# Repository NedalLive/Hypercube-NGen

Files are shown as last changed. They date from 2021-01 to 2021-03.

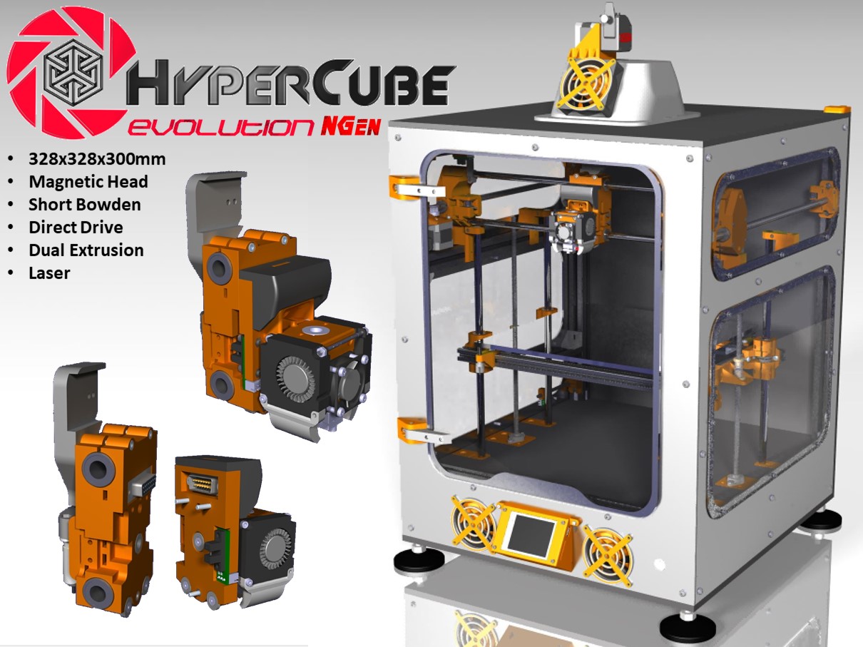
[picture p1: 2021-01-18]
Hypercube NGEN V2/images/Montage Hypercube V2.jpg

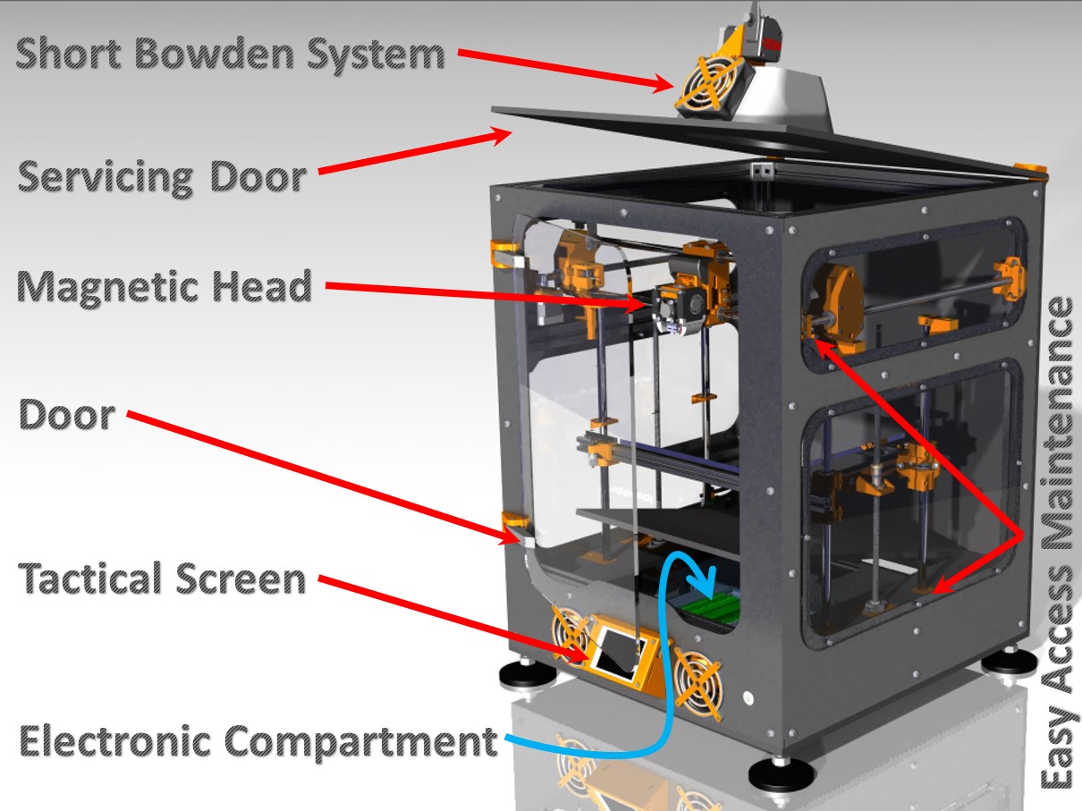
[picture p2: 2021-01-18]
Hypercube NGEN V2/images/montage Hypercube V22.jpg

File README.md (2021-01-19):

Logo Ngen

### **La Machine:**
Capture3

### Les têtes d'origine
Ngen V2 All Head Front

### Hypercube Ngen (NedalLive Genertion) 300x300x300

* Bowden Court de 400mm.
* Caisson fermé integralement.
* Tête Magnétique à remplacement rapide
* MultiTêtes develloppées par la communauté
* Bowden
* Direct Drive BMG, Titan aero et Hemera
* Hotend E3DV6
* Hotend AIO
* Hotend Dragon
* Gravage Laser
* Evolution constante

Un kit châssis disponible sur le site http://www.systeal.com/fr/kits-imprimantes-3d/1242-kit-hypercube-evo-ngen.html
Les plaques Dibond peuvent être commandées chez https://gen3d.fr/categoaquarie-produit/plge-hypercube-ngen/

Hypercube Ngen C'est vous, C'est nous! continuons à faire évoluer la machine !
Les idées les plus folles sont les bienvenues:
https://www.facebook.com/groups/hypercubeevolutionfr/
https://www.facebook.com/groups/Hypercubeevolution/

Pour conclure : je tiens à rappeler que nous sommes bénévoles et que ce n'est pas notre travail, nous sommes comme vous tous qui passez par ici, je vous remercie donc par avance pour votre bienveillance et votre participation active à l'évolution du bébé.

Pour me Soutenir:



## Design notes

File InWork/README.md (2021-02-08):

__Le contenu de ce dossier n'est pas encore Partagé, il est reservé à l'equipe de Dev. c'est à vos risques et periles !__

## Pour les Developpeurs
Creer un dossier pour chaques sujet en cour de Dev.
Y ajouter un README.md qui contien une explication succinte du projet en cours

## Explication de l'arborescence des Repères
Les N° de Repere de 0001 a 0999 sont des pièces Fabriquées
Les N° de Repere de 1000 à 9999 sont des Elements standards (acheter)

* A001 - Chassis
  * C001 Support Poulie AV V2
  * C002 Suppor Poulie AR V2

* A002 - Plateau
  * D00x - Reservé Dev Lié au plateau

* A003 - Axe Y
  * E00x - Reservé aux Dev liés à l'axe Y

* A004 - Axe X
  * B001 Chariot X
  * B002 Tête Piezo Orion E3DV6
  * B003 Tête E3DV6 standard
  * B004 Tête AIO Standard
  * B005 Tête Laser
  * B006 Tête Dragon

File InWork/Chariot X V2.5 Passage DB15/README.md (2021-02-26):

Simple modification pour pouvoir passer la prise DB15 DEJA CABLEE, au travers du chariot, en cas de changement (casse d'un élement du chariot).

Cela évite une étape "simple" mais très fastidieuse, le décablage total de la tête d'impression c.a.d. débrancher sur la carte mère, sortir les cables des passages de cables, des chaines, passer au travers du chariot, puis la même dans l'autre sens)
Quand on a un caisson, c'est un "life saver"

Il ya 2 versions : 
- V2, pour ceux qui ont des capteurs piezzo
- V1, pour ceux qui comme moi sont sur une V1 bltouch et n'ont pas l'intention de migrer vers la V2 dans l'immédiat.

La version V1 a été "améliorée" :
- relookage pour ressembler à la V2
- création de passages pour des boutons de serrage de roulement, sur la vis des aimants inférieurs  (le step des boutons est inclus)
- prévu pour les aimants supermagnete CS-S-15-04-N

NOTA : il y a une paroi fine, pour l'écrou de l'aimant central, à voir si ça peut s'imprimer correctement (pour la V1 ça passe !)

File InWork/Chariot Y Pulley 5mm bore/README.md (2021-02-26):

Modification des chariots Y :

Utilisation de poulies (de marques Mellow) 2GT alésage de 5mm pour courroie de 6mm

Alignement des poulies des chariots Y avec les nouveaux supports de poulies AV/AR

Assurez vous d'avoir une imprimante bien calibrée:

Réglage des steps de l'extrudeur

Réglage du débit de l'extrudeur

Réglage recommandé du Slicer:

Buse : 0,4mm

Hauteur de couche : 0,20mm

Nombre de périmètre : 4

Remplissage : 25%

Attention au sens d'impression des chariots, regardez la capture d'écran disponible montrant le sens d'impression

Modification of Y carriages:

Use of pulleys (Mellow brands) 2GT 5mm bore for 6mm belt

Alignment of carriage pulleys with new front / rear pulley brackets

Make sure you have a well calibrated printer:

Adjustment of extruder steps

Adjustment of extruder flow

Recommended slicer setting:

Nozzle: 0.4mm

Layer height: 0.20mm

Number of perimeter: 4

Infill: 25%

Pay attention to the printing direction of the carriages, see the screenshot available showing the printing direction

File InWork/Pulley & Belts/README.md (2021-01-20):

## Dev Poulies Courroies
* Demultiplication 20/30 dents
* Transfert des moteur à l'arriere sur SilentBlock
* ReDesign des supports poulies AR et AV
* Passage de toute les poulies sur Diametre interieur 5mm

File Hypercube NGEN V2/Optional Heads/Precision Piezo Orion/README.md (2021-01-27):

https://www.thingiverse.com/thing:4014481

compatible NGEN V2 en enlevant le endstop

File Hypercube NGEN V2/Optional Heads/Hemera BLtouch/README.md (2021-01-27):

Hemera for HEVO NGEN first generation by pipersw on Thingiverse: https://www.thingiverse.com/thing:4695196

Based on "E3d Hemera Mount for Precision Orion Piezo - Hypercube Evolution - HEVOHemera Piezo Orion for NGEN first gen"
https://www.thingiverse.com/thing:4694110
I design my own head for E3D Hemera/ Trianglelabs matrix extruder for the HEVO NGEN first generation.

The fan shroud is just take from "5015 Hemera Fan Shroud with BLTouch bracket" https://www.thingiverse.com/thing:4588159

The Offset position of the bltouch will be: X-24.50 Y-44.00 Z-0.95

The Hemera model is from "E3D Hermes / Hemera CAD (V6&Volcano)" https://www.thingiverse.com/thing:4025946

The Matrix extruder is more or less a clone of the hemera extruder. The position of the nozzle is not exactly the same.
5015 Fan Shroud for Matrix Extruder https://www.thingiverse.com/thing:4722064

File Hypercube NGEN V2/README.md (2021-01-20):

### la têtes principale V2 vue en coupe
TETE PIEZO COUPEE

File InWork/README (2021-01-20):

## Dossier de travail des developpeur##
Le contenue de ce dossier n'est pas encore Partagé c'est à vos risques et periles !

##Pour les Developpeur##
Creer un dossier pour chaques sujet en cour de Dev
Y ajouter un README qui contien une explication succinte du projet en cours

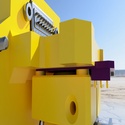
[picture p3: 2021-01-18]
Hypercube NGEN V2/Optional Heads/Precision Piezo Orion/images/large_thumb_2.jpg

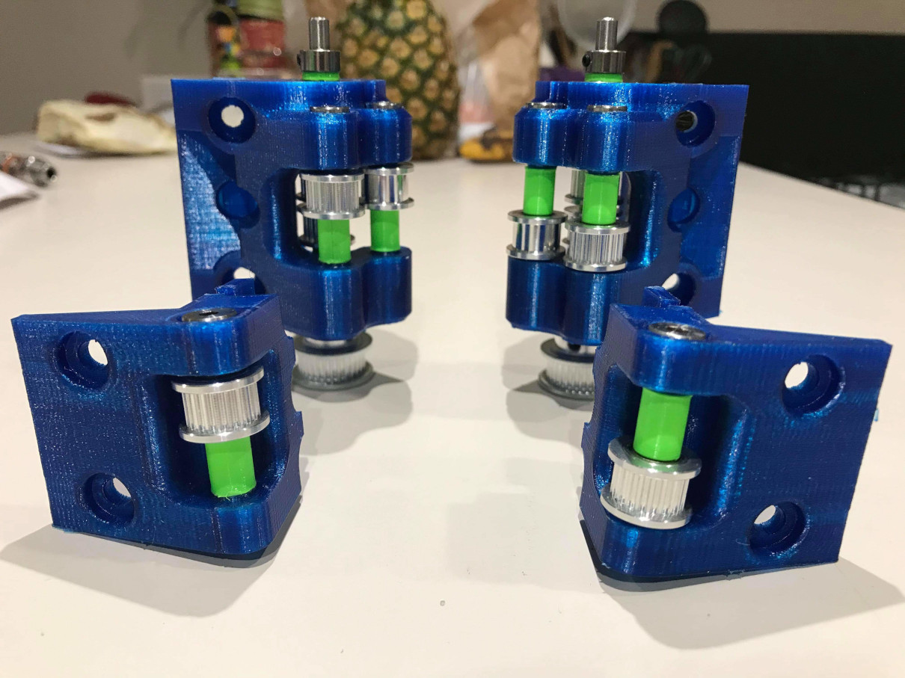
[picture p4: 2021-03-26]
InWork/Pulley & Belts/Images/vue de 4 supports.jpeg

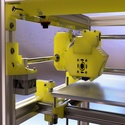
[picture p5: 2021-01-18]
Hypercube NGEN V2/Optional Heads/Precision Piezo Orion/images/large_thumb_9.jpg

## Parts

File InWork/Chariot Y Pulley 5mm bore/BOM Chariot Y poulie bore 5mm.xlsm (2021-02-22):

Désignations | Quantité | Liens d'achat
Vis epaulée Diametre 5 M4 x 25mm (25mm longeur de l'épaulement) | 4 | https://fr.aliexpress.com/item/4000704090811.html?spm=a2g0o.cart.0.0.47e73c00lnQyEg&mp=1
Ecrou M4 | 4 | https://fr.aliexpress.com/item/32977174437.html
Poulie Mellow GT2 6mm alésage 5mm 20 dents | 2 | https://fr.aliexpress.com/item/33023133633.html?spm=a2g0o.cart.0.0.1a143c00NBzYn4&mp=1
Poulie Mellow GT2 6mm alésage 5mm sans dent | 2 | https://fr.aliexpress.com/item/33023133633.html?spm=a2g0o.cart.0.0.1a143c00NBzYn4&mp=1

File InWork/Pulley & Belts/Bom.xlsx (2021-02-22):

support poulie AR LR | Qté | Lien
Bering 625zz | 4 | https://fr.aliexpress.com/item/32816424545.html
Axe Diam 5 L90mm | 2 | https://fr.aliexpress.com/item/1005001279496068.html
Vis epaulé D5x40 M4 | 4 | https://fr.aliexpress.com/item/4000704090811.html?spm=a2g0o.cart.0.0.28963c00ZiA8Oa&mp=1
Ecrou M4 | 4 | https://fr.aliexpress.com/item/32798773566.html
Poulie libre Gates 20T Bore 5 | 4 | https://fr.aliexpress.com/item/33023133633.html
Poulie libre Gates 20WT Bore 5 | 2 | https://fr.aliexpress.com/item/33023133633.html
Poulie Fixe Gates 20T Bore 5 | 2 | https://fr.aliexpress.com/item/4001045520299.html?spm=a2g0s.9042311.0.0.7a326c37pw91rd
Poulie Fixe Gates 30T Bore 5 | 2 | https://fr.aliexpress.com/item/4001308821466.html?spm=a2g0o.cart.0.0.28963c00ZiA8Oa&mp=1
Anneau de verouillage D5 x7.5mm | 2 | https://fr.aliexpress.com/item/32900283591.html?scm_id=1007.14976.205978.0&scm-url=1007.14976.205978.0&_t=gps
Vis M3x18 | 4
Ecrou M3 | 4
Courroie GT2 Close L154mm (ou entre 150 et 160) | 2 | https://fr.aliexpress.com/item/4000311901856.html
Amortisseur Nema17 | 2 | https://www.aliexpress.com/item/4000114726218.html?spm=a2g0s.9042311.0.0.2cc84c4dCTUro2
Spacer 72 | 4 | imprimé
Spacer 73 | 4 | imprimé
Spacer 74 | 2 | imprimé
Spacer 75 | 4 | imprimé
Support Poulie AV LR
Vis épaulé D5x30 M4 | 2 | https://fr.aliexpress.com/item/4000704090811.html?spm=a2g0o.cart.0.0.28963c00ZiA8Oa&mp=1
Poulie Libre 20T Bore 5 | 2 | https://fr.aliexpress.com/item/33023133633.html
Ecrou M4 | 2 | https://fr.aliexpress.com/item/32798773566.html
Vis M3x18 | 4
Ecrou M3 | 4
Spacer 73 | 2 | imprimé

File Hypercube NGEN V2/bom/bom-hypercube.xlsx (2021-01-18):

BOM BY MICHAEL HAM | will not be kept up to date / For Information
designation | for information | quantité | reference | fournisseur | lien | PRIX | remarque
ventilateur moteur | 50mm 12vdc | 2 |  |  | https://fr.aliexpress.com/item/New-Plastic-DC-12V-2-Pins-Connector-Brushless-Cooling-Fan-50mm-x-50mm-x-10mm/32747373317.html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 | 1.6
boutton on/off | m16 | 1 | 220vac |  | https://fr.aliexpress.com/item/1PCS-YT1211-Hole-Size-16-mm-Self-locking-Latching-switch-Metal-push-button-switch-With-LED/32789229044.html | 4.14
connecteur db15f |  | 1 | d-sub DB15F |  | https://fr.aliexpress.com/item/Promotion-DB15-15-Pin-Female-to-Male-Solder-Type-Adapter-Connectors-5-Pair/32623042100.html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 | 1.79
connecteur db15m |  | 1 | d-sub DB15M |  |  | 0 | en kit au dessus
bornier |  | 5x10 | UK2,5N | LEGRAND | https://fr.aliexpress.com/item/10Pcs-UK-3N-Instead-of-PHOENIX-CONTACT-Terminal-Blocks-DIN-Rail-Universal-Class-Connector-Screw-Terminal/32875022823.html | 14.32
Bltouch |  | 1 |  | antclabs | https://fr.aliexpress.com/item/3D-Touch-Auto-Leveling-Sensor-Auto-Bed-Leveling-Sensor-BLTouch-For-3D-Printers-Improve-Printing-Precision/32890485972.html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 | 10.5
extrudeur |  | 1 | BMG | Bontech | https://fr.aliexpress.com/item/Prusa-i3-mk2-mk2-5-mk3-3d-imprimante-extrudeuse-engrenages-d-entra-nement-Btech-double-engrenages/32898104617.html | 10.16 | c'est les roulements le reste est a imprimer ou http://urlz.fr/7HNY ou http://urlz.fr/7HO3
E3DV6 ou AIO |  | 1 |  | E3D ou hotend,fr | https://fr.aliexpress.com/item/E3DV6-12-v-distance-0-4-1-75-4-1-gorge-tout-droit-travers-5-gorge/32895173407.html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 | 13.57
ventilateur boitier | 80mm 12vdc | 3 |  |  | https://fr.aliexpress.com/item/80-80-25-MM-Personal-Computer-Case-Cooling-Fan-DC-12V-2200RPM-45CM-Fan-Cable-PC/32785097667.html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 | 3.18
ventilateur radial | 4010 12VDC | 2 |  |  | http://urlz.fr/7HO9 | 5.52
relais ssr |  | 1 | SSR 12DC 220AC |  | https://fr.aliexpress.com/item/1pcs-solid-state-relay-SSR-25DA-25A-3-32V-DC-TO-24-380V-AC-SSR/32663806352.html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 | 2.61
dual relais |  | 1 | 5VIN 12VDC |  | https://fr.aliexpress.com/item/3-3-v-5-v-12-v-24-v-4-Canal-Relais-Module-Haute-et-faible/32880648815.html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 | 6,22/5,96 | est ce bon ? Et surtout lequel 5v ou 12 v? | 6.22
Ressort | 7,5x5x20mm | 4 |  |  | https://fr.aliexpress.com/item/10-Pcs-Carbon-Steel-Feeder-Spring-For-Makerbot-3D-Printer-Extruder-Heated-Bed-W315/32818242357.html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 | 0.91
raspberry pi3 |  | 1 |  | RASPBERRY | https://fr.aliexpress.com/item/2016-NEW-Original-Raspberry-Pi-3-Model-B-Board-1GB-LPDDR2-BCM2837-64-bit-Quad-Core/32626862737.html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 | 37.61
allimentation |  | 1 | 220AC 12DC 500W |  | https://fr.aliexpress.com/item/Szvfun-50W-Led-Driver-100w-220v-to-12v-10A-Power-Supply-12v-5A-15A-20A-30A/32843698051.html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 | 24.73
FIN DE COURSE |  | 3 | OPTICAL SENSOR |  | https://fr.aliexpress.com/item/HAILANGNIAO-6pcs-lot-Optical-Endstop-Light-Control-Limit-Optical-Switch-for-3D-Printers-RAMPS-1-4/32870806194.html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 | 2.53
RAIL DIN | 185mm | 2 | DIN |  | https://www.amazon.fr/sourcingmap%C2%AE-coulissant-Design-montage-Coupe-circuit/dp/B0159MTN2O | 5.22
MOTEUR |  | 5 | 17HS44001 |  | https://www.amazon.fr/TopDirect-Moteur-56-2oz-2-Phase-imprimante/dp/B075JG2MVS | 42.99
POULIE AVEC DENTS |  | 6 | GT2 W6 B3 20T |  | https://fr.aliexpress.com/item/GT2-Poulie-16-20-Sans-Dents-Poulie-16-20-Dents-OU-Sans-Dents-Pignon-de-distribution/32856650625.html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 | 3.66 | 20t 3x6 with
POULIE SANS DENTS |  | 2 | GT2 W6 B3 WT |  | https://fr.aliexpress.com/item/GT2-Poulie-16-20-Sans-Dents-Poulie-16-20-Dents-OU-Sans-Dents-Pignon-de-distribution/32856650625.html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 | 1.22 | 20t 3x6 without
POULIE MOTEUR |  | 2 | GT2 20T |  | https://fr.aliexpress.com/item/Gt2-Poulie-20-dents-Al-sage-5mm-6mm-6-35mm-8mm-pour-Largeur-6mm-GT2-synchrone/32881567459.html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 | 2x 3,16 | prendre en 2 x 3 pour eviter les fdp
CARTE MERE REARM RAMP 1,6 |  | 1 | REARM + RAMP1,6 |  | https://fr.aliexpress.com/item/Rampes-1-6-carte-de-mise-niveau-base-sur-Rampes-1-4-1-5-Mega-2560/32855234226.html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 | 31.37 | a4988 ou 52,94€ pour des tmc2208
ECRAN TFT3,2 |  | 1 | TFT32 | MKS | https://fr.aliexpress.com/item/CE-RoHS-3D-Printer-splash-screen-MKS-TFT32-touch-screen-smart-controller-display-3-2inch-support/32808866999.html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 | 25.76
MOSFET HOTEND | 12VDC 12/24VDC | 1 |  | MKS MOSFET | https://fr.aliexpress.com/item/3D-printer-parts-heating-controller-MKS-MOSFET-for-heat-bed-extruder-MOS-module-exceed-30A-support/32753129988.html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 | 7.67 | ou 2,70 ici =>https://fr.aliexpress.com/item/New-Hot-3D-Printer-Accessories-Mosfet-Heated-Bed-Power-Module-MKS-for-Anet-A8-A6-A2/32890179872.html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
AIMANT PLAT FRAISE | ⌀12x3 | 3 | 41-243-12 | EMILE MAURIN | https://fr.aliexpress.com/item/10-Pieces-pack-12-x-3-mm-Magnet-Strong-Neodymium-Magnets-Permanent-N50-Magnetic-Materials/32811494867.html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 | 18,4/3,13 | (version EMILE MAURIN) / (version aliexpress)
SUPPORT POUR AIMANT | ⌀12x2 | 3 | 41-600-12 | EMILE MAURIN | https://fr.aliexpress.com/item/50pcs-12mmx2mm-12X2mm-Super-Strong-Round-Disc-Rare-Earth-Neodymium-magnet-12-2-NEW-Art-Craft/32807408402.html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 | 5,55/1,66 | (version EMILE MAURIN) / a percer(version aliexpress)ou des rondelles fraisé
CANON DE GUIDAGE | ⌀2,9x8 | 1 | 33-041-6 2,9 8 | EMILE MAURIN | fdp 20,1 | 7,95/? | (version EMILE MAURIN) soit total 52€ / pas trouvé sur ali
VIS BHC | M5x10 | 41 | ISO7380 |  | https://fr.aliexpress.com/item/50-PCS-ISO7380-En-Acier-Inoxydable-a2-70-M5-10-m5-x-10-Six-Pans-Creux/32841075185.html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 | 3.64
VIS BHC | M5x16 | 25 | ISO7380 |  | https://fr.aliexpress.com/item/AXK-50pcs-M5-Alloy-Steel-ISO7380-Metric-Thread-Button-Head-Hex-Socket-Cap-Screws-Round-Bolts/32869792263.html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 | 5.53
VIS BHC | M5x12 | 74 | ISO7380 |  | https://fr.aliexpress.com/item/AXK-50pcs-M5-Alloy-Steel-ISO7380-Metric-Thread-Button-Head-Hex-Socket-Cap-Screws-Round-Bolts/32869792263.html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 | 9.94 | en prendre 2
VIS BHC | M3x8 | 16 | ISO7380 |  | https://fr.aliexpress.com/item/AXK-100pcs-Grade10-9-iso7380-M3-3-4-5-6-8-10-12-14-16-18/32870504082.html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 | 1.21
VIS BHC | M3x30 | 8 | ISO7380 |  | https://fr.aliexpress.com/item/100pcs-Grade10-9-iso7380-M3-3-4-5-6-8-10-12-14-16-18-20/32781852232.html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 | 3.34
VIS BHC | M3x25 | 2 | ISO7380 |  | https://fr.aliexpress.com/item/100pcs-Grade10-9-iso7380-M3-3-4-5-6-8-10-12-14-16-18-20/32781852232.html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 | 3.34
VIS BHC | M3x20 | 37 | ISO7380 |  | https://fr.aliexpress.com/item/100pcs-Grade10-9-iso7380-M3-3-4-5-6-8-10-12-14-16-18-20/32781852232.html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 | 3.15
VIS BHC | M3x16 | 36 | ISO7380 |  | https://fr.aliexpress.com/item/100pcs-Grade10-9-iso7380-M3-3-4-5-6-8-10-12-14-16-18-20/32781852232.html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 | 1.9
VIS BHC | M3x12 | 56 | ISO7380 |  | https://fr.aliexpress.com/item/100pcs-Grade10-9-iso7380-M3-3-4-5-6-8-10-12-14-16-18-20/32781852232.html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 | 2.52
VIS BHC | M2,5x16 | 2 | ISO7380 |  | https://fr.aliexpress.com/item/100PCS-ISO7380-M2-5-3-4-5-6-8-10-12-14-16-18-20-22/32803284037.html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 | 2.23
VIS BHC | M2,5x8 | 2 | ISO7380 |  | https://fr.aliexpress.com/item/100PCS-ISO7380-M2-5-3-4-5-6-8-10-12-14-16-18-20-22/32803284037.html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 | 1.48
ECROU | M3 | 105 |  |  | https://fr.aliexpress.com/item/M3-nut-M3-copper-column-matching-hex-nut-nut/32756822044.html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 | 1.74 | en prendre 2
GOUJON | M2,5x50 | 1 |  |  | https://fr.aliexpress.com/item/12-9-Level-Cylindrical-Head-Six-Angle-Bolt-M2-5-50/32721234193.html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 | 1.75 | pas obligatoire
VIS TRAPEZOIDALE Z | M8x2x395 | 2 |  |  | https://fr.aliexpress.com/item/3D-Printer-THSL-300-8D-Lead-Screw-Dia-8MM-Pitch-1mm-Lead-1mm-Length-300mm-with/32722807591.html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 | 13.7
ECROU | M2,5 | 6 |  |  | https://fr.aliexpress.com/item/50-Pcs-DIN934-M2-M2-5-M3-M4-M5-M6-M8-Noir-Nylon-crou-Hexagonal-Hexagone/32874859068.html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 | 0.75
RONDELLE 5mm | ⌀5x2,8 | 35 | ISO7089 |  | https://fr.aliexpress.com/item/100Pcs-DIN125-ISO7089-M1-6-M2-M2-5-M3-M3-5-M4-M5-M6-M8-M10/32795320300.html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 | 1.92
RONDELLE 3mm | ⌀3x0,6 | 32 | ISO7089 |  | https://fr.aliexpress.com/item/100Pcs-DIN125-ISO7089-M1-6-M2-M2-5-M3-M3-5-M4-M5-M6-M8-M10/32795320300.html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 | 1.31
VIS FHC | M3x10 | 4 | DIN7991 |  | https://fr.aliexpress.com/item/100pcs-lot-DIN7991-M3-4-5-6-8-10-12-14-16-20-Stainless-Steel-304/32785914892.html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 | 2.09
VIS FHC | M3x50 | 4 |  |  | https://fr.aliexpress.com/item/M3-DIN7991-10-9-Flat-Head-Cap-Screws-Countersunk-Head-Cap-Screws-Flat-Cup-Screws-M3/32841370184.html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 | 1.67
VIS FHC | M3x30 | 2 | DIN7991 |  | https://fr.aliexpress.com/item/50pcs-lot-DIN7991-M3-4-5-6-8-10-14-12-16-20-25-30-m3/32852869121.html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 | 2.94
T8 ECROU ANTIBACKLASH | 8x2mm | 2 |  |  |  | 0 | compris avec les vis trapezoidale
PLATEAU | 328x328x EP3 | 1 | MK2A |  | https://fr.aliexpress.com/item/2017-MK2A-300-300-3-0mm-RepRap-RAMPS-1-4-PCB-Aluminum-Heatbed-Hot-Plate-For/32811352753.html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 | 26.31
LIT CHAUFFANT SILICON | 300x300 | 1 | 220V AC |  | https://fr.aliexpress.com/item/Silicone-coussin-chauffant-chauffe-200x200-220-220-300x300mm-Puissance-160-w-280-w-360-w-500/32882403658.html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 | 20.02
PALLIER Z | ⌀8 | 2 | KFL08 |  | https://fr.aliexpress.com/item/2Pcs-KFL08-Pillow-Block-Bearing-8mm-Bore-Diameter-Zinc-Alloy-Rhombic-Flange-Bearing-For-CNC/32793159224.html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 | 2.05
ACCOUPLEMENT FLEXIBLE Z | D20L25 5x8 | 2 | RB | MISUMI | https://fr.aliexpress.com/item/1-pcs-D20L25-5X8mm-En-Alliage-D-aluminium-Z-Axe-Flexible-Accouplement-Pour-Moteur-pas-pas/32876571198.html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 | 5.38 | prendre en 2 commandes pour eviter les fdp
DOUILLE A BILLE Z |  | 8 | LM12UU | MISUMI | voir avec https://www.facebook.com/henri.rodat?sk=wall&fref=gs&dti=245503589286876&hc_location=group_dialog | 36 | 4,5*8
DOUILLE A BILLE Y |  | 2 | LM10LUU | MISUMI | fdp 3,7 | 15 | 7,5*2
DOUILLE A BILLE X |  | 4 | LM10UU | MISUMI | total 72,7 | 18 | 4,5*4
AXE DE GUIDAGE Z | ⌀12x400 | 4 | ACIER CALIBRE | MISUMI | https://fr.aliexpress.com/item/12mm-linear-shaft-200-300-350-400-440-500-560-600-650-800-mm-Chromed-Hardened/32858883464.html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 | 27.6 | ou a voir sur dold mechatronik,de https://www.dold-mechatronik.de/navi.php?a=1457&lang=eng
AXE DE GUIDAGE Y | ⌀10x450 | 2 | ACIER CALIBRE | MISUMI | https://fr.aliexpress.com/item/Optical-Axis-300-320-350-380-400-450-500-mm-Smooth-Rods-8mm-Linear-Shaft-Rail/32882612771.html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 | 12.3 | en tout 64,9 sur dold
AXE DE GUIDAGE X | ⌀10x480 | 2 | ACIER CALIBRE | MISUMI | https://fr.aliexpress.com/item/Optical-Axis-300-320-350-380-400-450-500-mm-Smooth-Rods-8mm-Linear-Shaft-Rail/32882612771.html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 | 12.6 | a recouper ou sinon au pire il peuve depasser dans le compartiment electronique
GOULOTTE ELEC | 25x25x200 | 5 |  |  | ? | ? | a prendre dans un leroymerlin
PIED | M8x50x⌀29 | 4 | PIED-D29-M8-50 | SYSTEAL |  | 0 | avec le kit
L-JOINT 3030 |  | 22 | EQ-P8-3030-INT-TPM | SYSTEAL | https://fr.aliexpress.com/item/10pcs-30-series-L-Shape-Type-Interior-Inner-Corner-Connector-Joint-Bracket-for-3030-Aluminum-Profile/32869698160.html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 | 19.86 | en prendre 3 ou alors prendre ici=> https://fr.aliexpress.com/item/20-pcs-L-Forme-Noir-Int-rieure-Coin-Connecteur-Conjointe-Support-pour-2020-3030-S-rie/32888059127.html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
EQUERRE 3030 |  | 10 | AKOYPKY6-TPM | SYSTEAL |  | 0 | avec le kit
EQUERRE2020 |  | 4 | AKOYPKY5 | SYSTEAL |  | 0 | avec le kit
T-NUT 3030 M5 |  | 100 | ECR-MA-P8-5 | SYSTEAL | https://fr.aliexpress.com/item/Free-shipping-100pcs-30-M5-hammer-nut-M5-block-t-slot-nuts-for-3030-aluminum-profile/32831895270.html | 8.66
T-NUT 2020 M5 |  | 50 | ECR-MA-P6-5 | SYSTEAL | https://fr.aliexpress.com/item/50PCS-20-m3-M4-M5-T-nut-Hammer-Head-Fasten-Nut-3D-Printer-Parts-Nickel-Plated/32909750370.html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 | 2.16
PROFILE 3030 Z | 30x30x640 | 4 | B-TYPE SLOT 8 | SYSTEAL | http://www.systeal.com/fr/kits-imprimantes-3d/1242-kit-hypercube-evo-ngen.html | 96.15
PROFILE 3030 Y | 30x30x460 | 8 | B-TYPE SLOT 8 | SYSTEAL |  | 0 | avec le kit
PROFILE 3030 X | 30x30x450 | 5 | B-TYPE SLOT 8 | SYSTEAL |  | 0 | avec le kit
PROFILE 2020 X | 20x20x446 | 2 | B-TYPE SLOT 6 | SYSTEAL |  | 0 | avec le kit
PROFILE 2020Y | 20x20x225 | 2 | B-TYPE SLOT 6 | SYSTEAL |  | 0 | avec le kit
courrroie gt2 6mm | 6mm*5m |  |  |  | https://fr.aliexpress.com/item/5m-lot-GT2-6mm-open-timing-belt-width-6mm-GT2-belt-Rubbr-Fiberglass-cut-to-length/32811832945.html | 2.8
total |  |  |  |  |  | 690.34 | il manque la goulotte

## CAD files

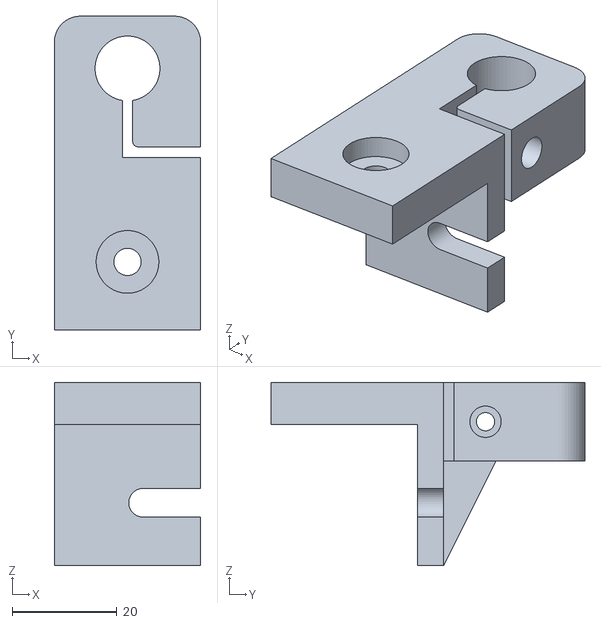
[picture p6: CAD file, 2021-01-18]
Hypercube NGEN V2/CAD/STL/A001 - ENSEMBLE CHASSIS/0020 - Z SUPPORT INF R.stl
28.0 x 60.0 x 35.0

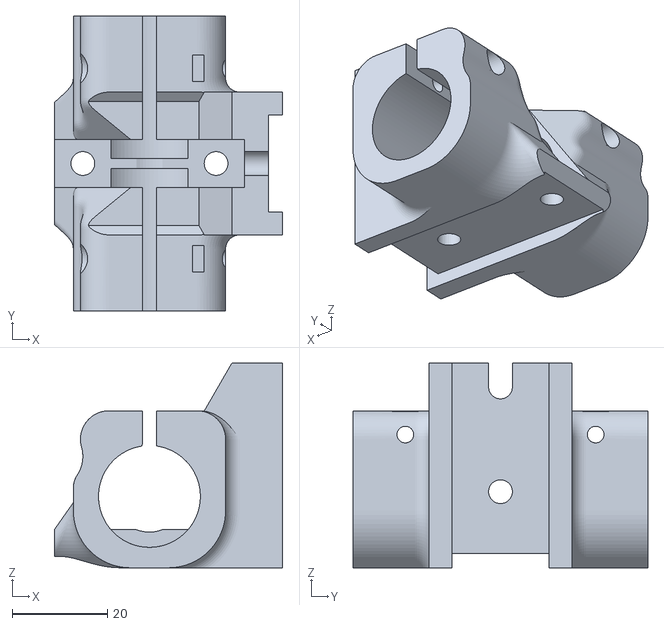
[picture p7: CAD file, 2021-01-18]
Hypercube NGEN V2/CAD/STL/A002 - ENSEMBLE PLATEAU/0023 - CHARIOT Z - LM12UU.stl
48.0 x 62.0 x 43.0

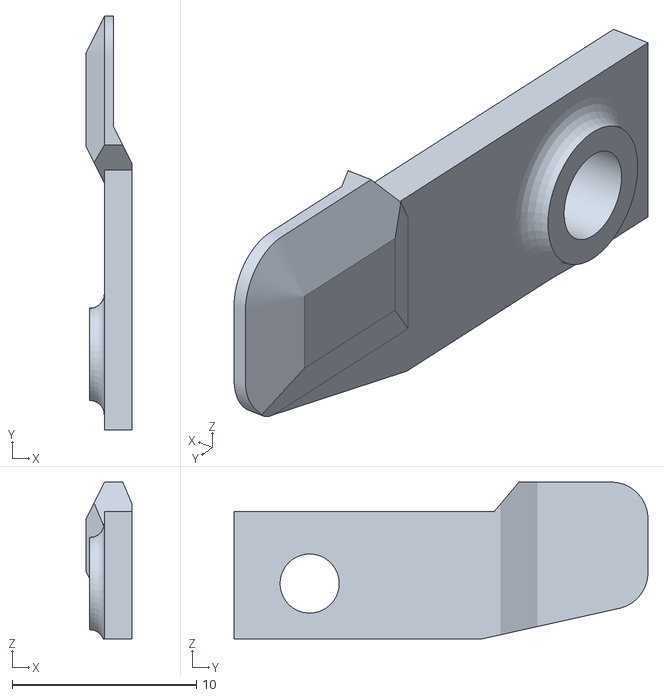
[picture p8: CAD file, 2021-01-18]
Hypercube NGEN V2/CAD/STL/A003 - ENSEMBLE AXE Y/0013 - DRAPEAU X.stl
2.50 x 22.4 x 8.50

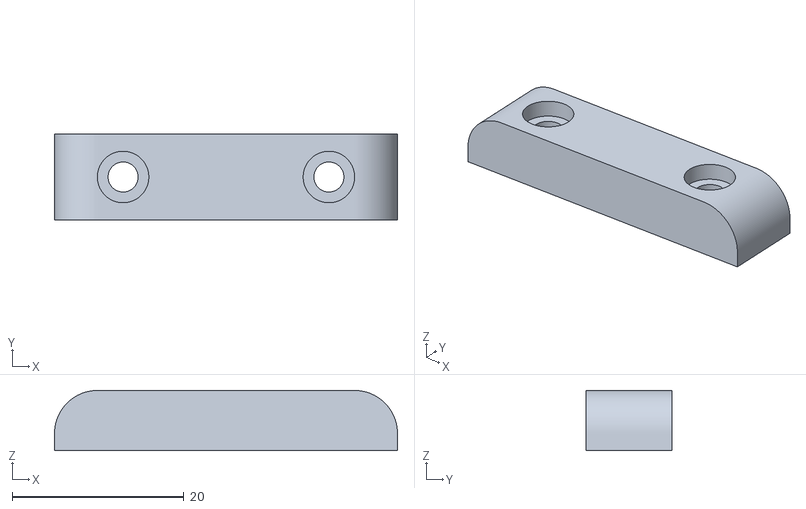
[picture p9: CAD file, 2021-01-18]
Hypercube NGEN V2/CAD/STL/A004 - ENSEMBLE AXE X/B001 - CHARIOT X V2/0002 - CLAMP.stl
40.0 x 10.0 x 7.00

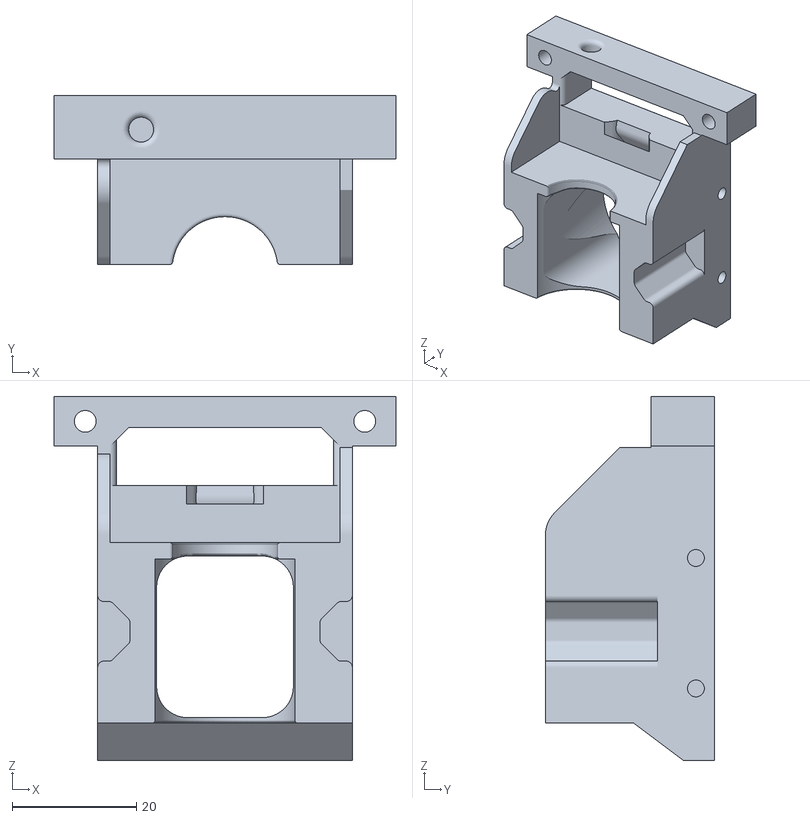
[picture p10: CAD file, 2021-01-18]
Hypercube NGEN V2/CAD/STL/A004 - ENSEMBLE AXE X/B002 - TETE PIEZO ORION/0007 - CLAMP 30mm TETE PIEZO E3DV6.stl
55.0 x 27.2 x 58.6

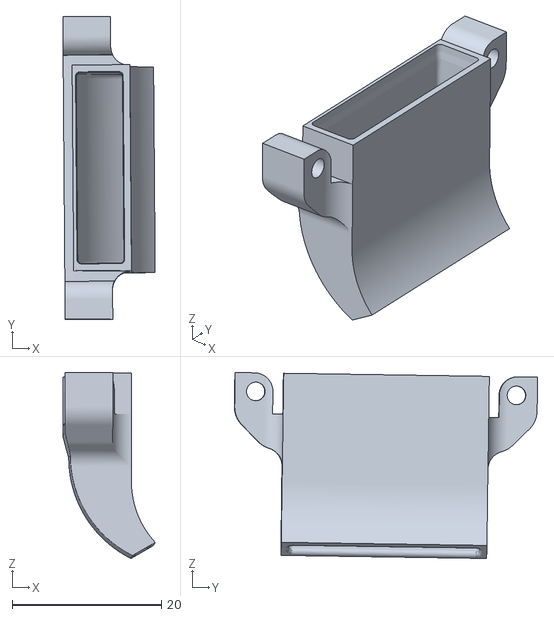
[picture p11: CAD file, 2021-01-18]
Hypercube NGEN V2/CAD/STL/A004 - ENSEMBLE AXE X/B003 - TETE E3DV6 STD V2/0009 - FAN DUCT STD.stl
12.4 x 40.7 x 25.0

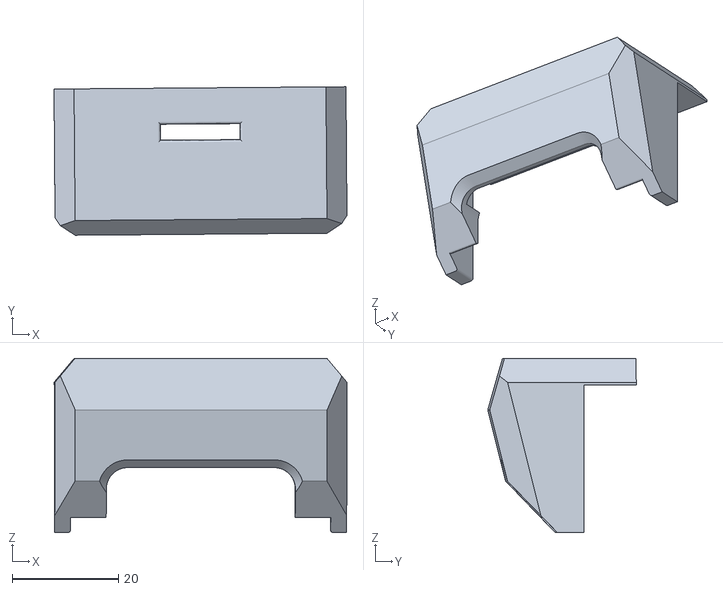
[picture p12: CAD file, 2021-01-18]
Hypercube NGEN V2/CAD/STL/A004 - ENSEMBLE AXE X/B004 - TETE AIO STD V2/0008 - CACHE STD.stl
55.2 x 28.0 x 32.8

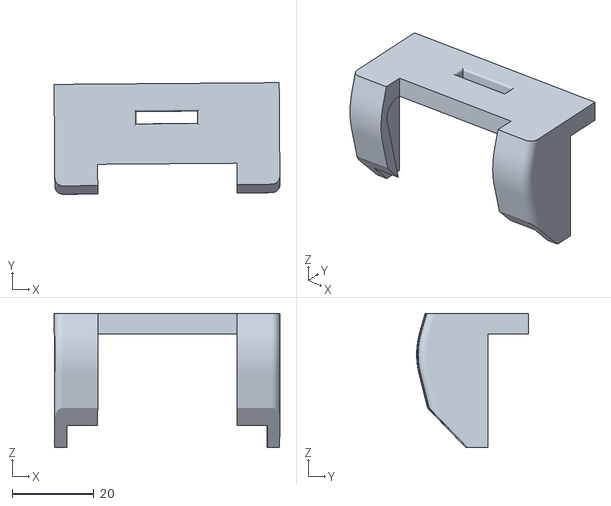
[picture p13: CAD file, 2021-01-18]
Hypercube NGEN V2/CAD/STL/A004 - ENSEMBLE AXE X/B005 - TETE LASER V2/0008 - CACHE LASER.stl
55.2 x 27.3 x 32.8

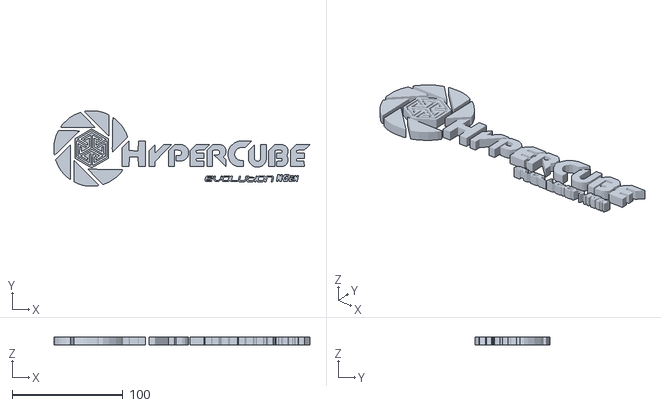
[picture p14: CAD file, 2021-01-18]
Hypercube NGEN V2/CAD/STL/HCEVO_NGEN.stl
231.1 x 67.8 x 6.98

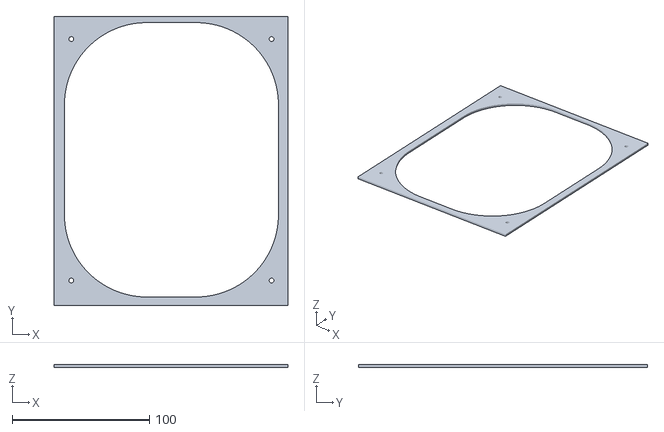
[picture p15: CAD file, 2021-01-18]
Hypercube NGEN V2/CAD/STL/Tips/PATRON DE DECOUPE PLANCHE SUP.stl
170.6 x 211.0 x 2.00

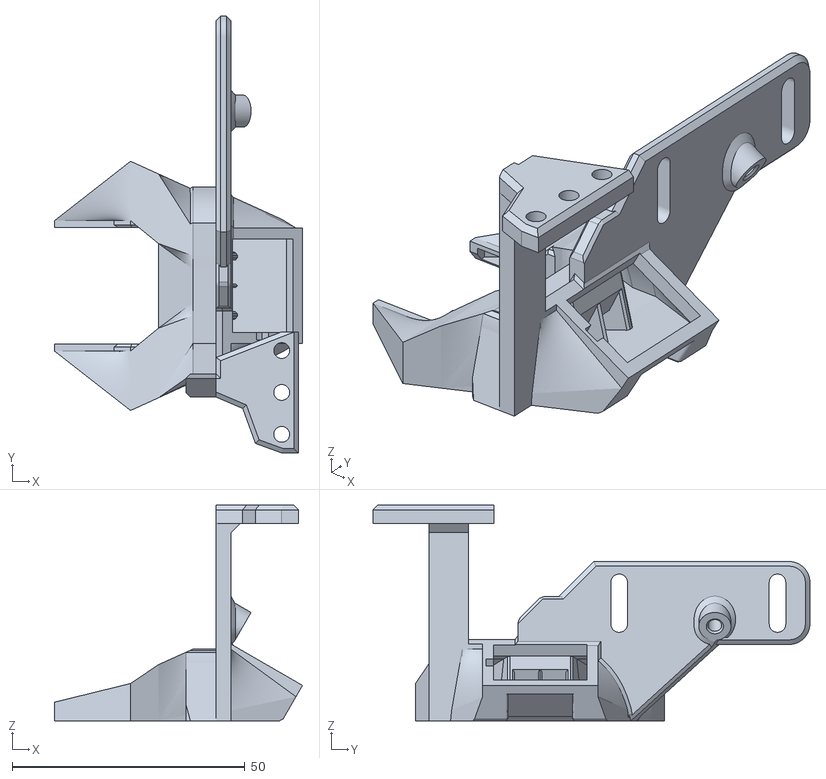
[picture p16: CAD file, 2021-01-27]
Hypercube NGEN V2/Optional Heads/Hemera BLtouch/STL/5015_Matrix_Shroud.stl
53.3 x 93.8 x 46.3

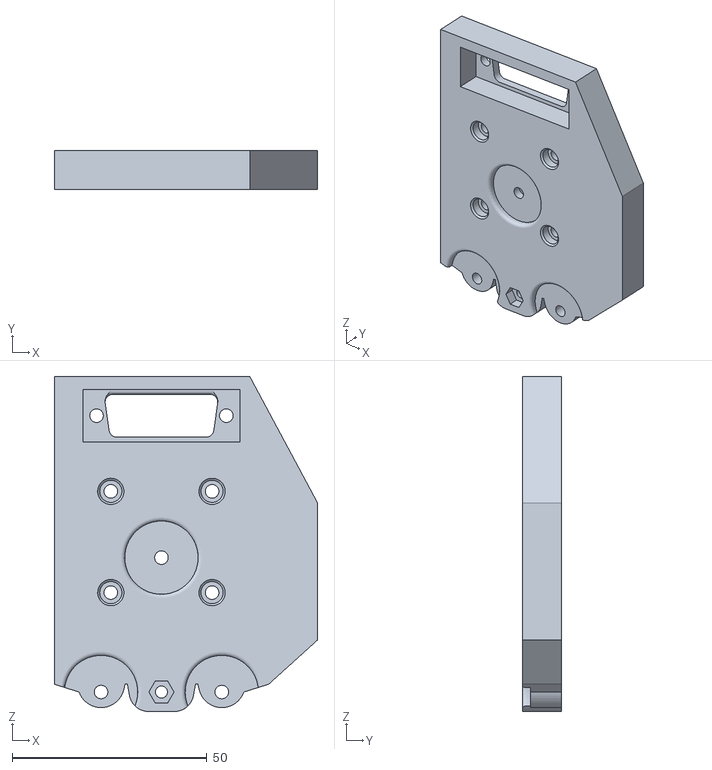
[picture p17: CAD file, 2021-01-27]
Hypercube NGEN V2/Optional Heads/Hemera Piezo Orion/STL/base Hemera piezo orion HEVO for NGEN V2.stl
67.6 x 10.0 x 86.0

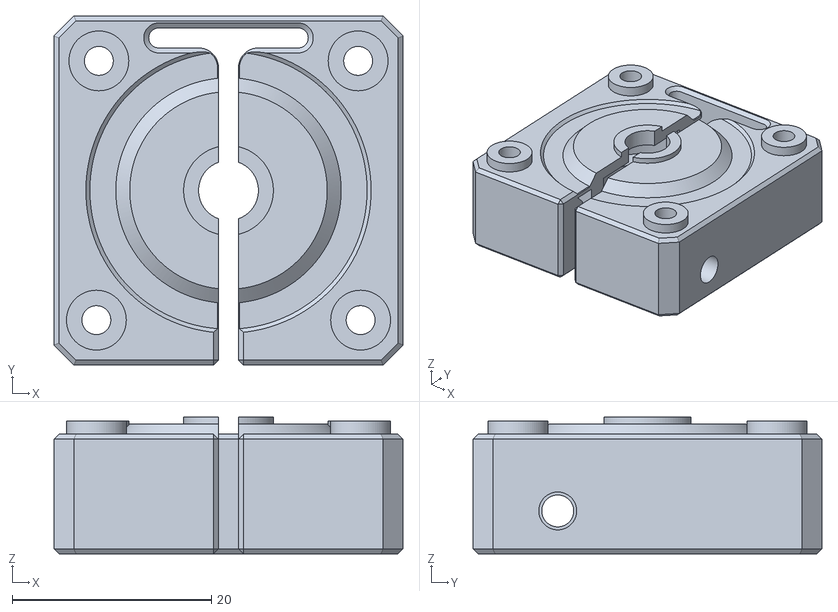
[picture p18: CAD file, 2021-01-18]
Hypercube NGEN V2/Optional Heads/Precision Piezo Orion/STL/Clamp_Precision_Orion_repaired.stl
35.0 x 35.0 x 13.7

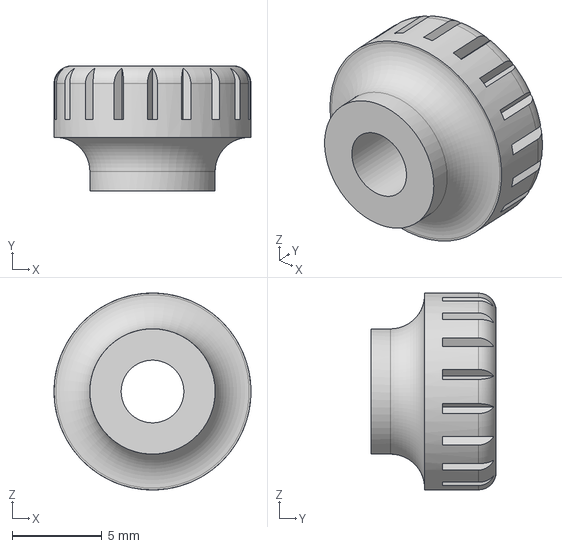
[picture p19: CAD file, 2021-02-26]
InWork/Chariot X V2.5 Passage DB15/STEP_HYPERCUBE-EVO-0001_NGENv1.5_bouton_serrage_roulement.step
11.0 x 7.00 x 11.0 mm

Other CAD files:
Hypercube NGEN V2/CAD/STL/A004 - ENSEMBLE AXE X/B006 - TETE PIEZO DRAGON V2/0007 - CLAMP 30mm TETE DRAGON V2.stl
InWork/Chariot Y Pulley 5mm bore/Chariot Y Right poulie bore 5mm.stl
InWork/Chariot Y Pulley 5mm bore/Version Step/Flag endstop X.step
InWork/Nova Hotend V1.1/STEP/HYPERCUBE-EVO-0006_NGEN_NOVA.stp
Hypercube NGEN V1/CAD/STEP/0006 - FOR DEVELLOPER.stp
Hypercube NGEN V1/CAD/STL/A001 - ENSEMBLE CHASSIS/0015 - SUPPORT MOTEUR XY L.stl
Hypercube NGEN V1/CAD/STL/A001 - ENSEMBLE CHASSIS/0016 - SUPPORT MOTEUR XY R.stl
Hypercube NGEN V1/CAD/STL/A001 - ENSEMBLE CHASSIS/0017 - SUPPORT POULIE AR L.stl
Hypercube NGEN V1/CAD/STL/A001 - ENSEMBLE CHASSIS/0018 - SUPPORT POULIE AR L.stl
Hypercube NGEN V1/CAD/STL/A001 - ENSEMBLE CHASSIS/0019 - Z SUPPORT INF L.stl
Hypercube NGEN V1/CAD/STL/A001 - ENSEMBLE CHASSIS/0021 - Z SUPPORT SUPP L.stl
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

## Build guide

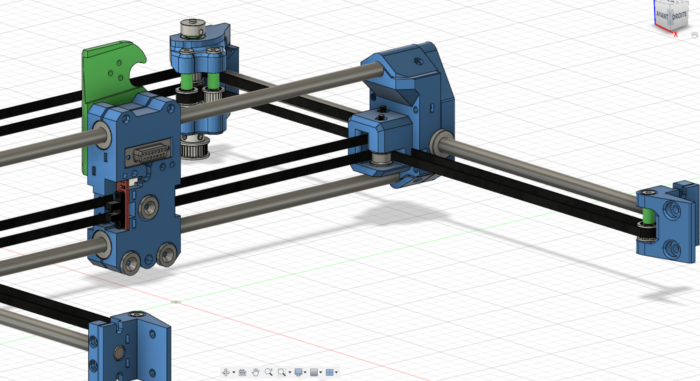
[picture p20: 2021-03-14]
InWork/Chariot Y Pulley 5mm bore/Image chariot Y/Chariot Y Right bore 5mm Assembly .png

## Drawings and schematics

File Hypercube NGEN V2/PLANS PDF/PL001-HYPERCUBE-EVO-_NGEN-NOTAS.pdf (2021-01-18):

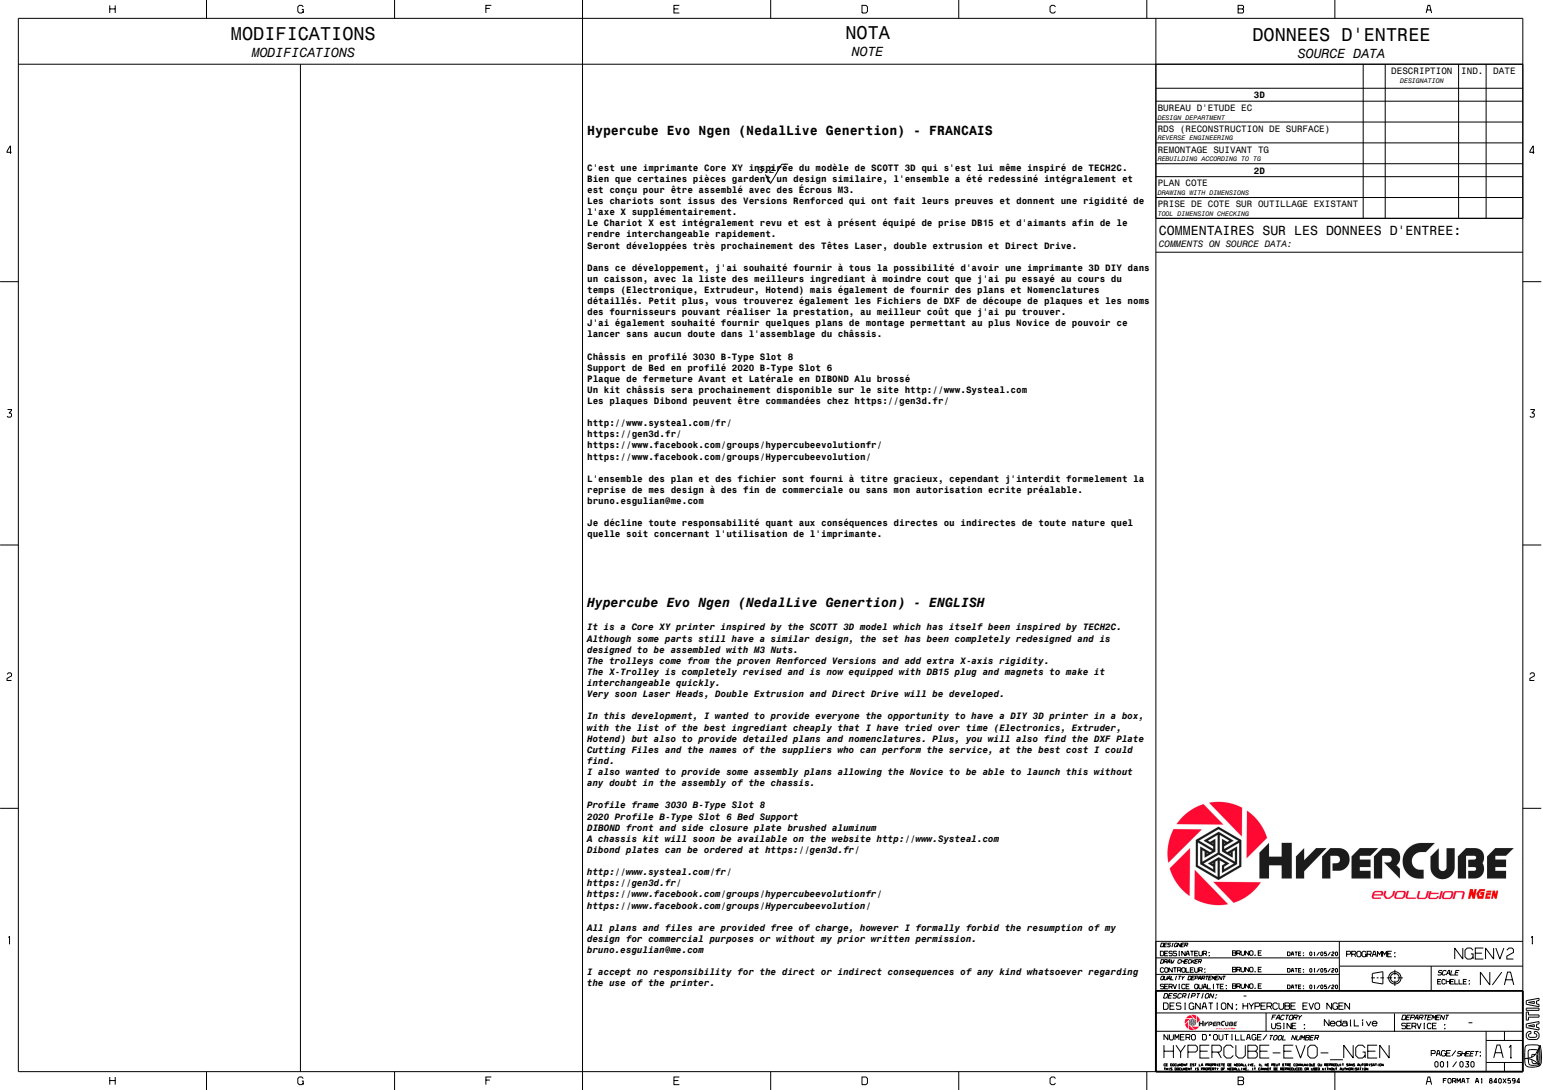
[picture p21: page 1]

MODIFICATIONS | NOTA NOTE | DONNEES D'ENTREE SOURCE DATA

DESCRIPTION DESIGNATION | IND. | DATE

BUREAU D'ETUDE EC DESIGN DEPARTMENT
RDS (RECONSTRUCTION DE SURFACE) REVERSE ENGINEERING
REMONTAGE SUIVANT TG REBUILDING ACCORDING TO TG

Hypercube Evo Ngen (NedalLive Genertion) - FRANCAIS

C'est une imprimante Core XY inspirée du modèle de SCOTT 3D qui s'est lui même inspiré de TECH2C.
Bien que certaines pièces gardent un design similaire, l'ensemble a été redessiné intégralement et
est conçu pour être assemblé avec des Écrous M3.
Les chariots sont issus des Versions Renforced qui ont fait leurs preuves et donnent une rigidité de
l'axe X supplémentairement.
Le Chariot X est intégralement revu et est à présent équipé de prise DB15 et d'aimants afin de le
rendre interchangeable rapidement.
Seront développées très prochainement des Têtes Laser, double extrusion et Direct Drive.

PLAN COTE DRAWING WITH DIMENSIONS
PRISE DE COTE SUR OUTILLAGE EXISTANT TOOL DIMENSION CHECKING

COMMENTAIRES SUR LES DONNEES D'ENTREE:
COMMENTS ON SOURCE DATA:

Dans ce développement, j'ai souhaité fournir à tous la possibilité d'avoir une imprimante 3D DIY dans
un caisson, avec la liste des meilleurs ingrediant à moindre cout que j'ai pu essayé au cours du
temps (Electronique, Extrudeur, Hotend) mais également de fournir des plans et Nomenclatures
détaillés. Petit plus, vous trouverez également les Fichiers de DXF de découpe de plaques et les noms
des fournisseurs pouvant réaliser la prestation, au meilleur coût que j'ai pu trouver.
J'ai également souhaité fournir quelques plans de montage permettant au plus Novice de pouvoir ce
lancer sans aucun doute dans l'assemblage du châssis.

Châssis en profilé 3030 B-Type Slot 8
Support de Bed en profilé 2020 B-Type Slot 6
Plaque de fermeture Avant et Latérale en DIBOND Alu brossé
Un kit châssis sera prochainement disponible sur le site http://www.Systeal.com
Les plaques Dibond peuvent être commandées chez https://gen3d.fr/

http://www.systeal.com/fr/
https://gen3d.fr/
https://www.facebook.com/groups/hypercubeevolutionfr/
https://www.facebook.com/groups/Hypercubeevolution/

L'ensemble des plan et des fichier sont fourni à titre gracieux, cependant j'interdit formelement la
reprise de mes design à des fin de commerciale ou sans mon autorisation ecrite préalable.
bruno.esgulian@me.com

Je décline toute responsabilité quant aux conséquences directes ou indirectes de toute nature quel
quelle soit concernant l'utilisation de l'imprimante.

Hypercube Evo Ngen (NedalLive Genertion) - ENGLISH

It is a Core XY printer inspired by the SCOTT 3D model which has itself been inspired by TECH2C.
Although some parts still have a similar design, the set has been completely redesigned and is
designed to be assembled with M3 Nuts.
The trolleys come from the proven Renforced Versions and add extra X-axis rigidity.
The X-Trolley is completely revised and is now equipped with DB15 plug and magnets to make it
interchangeable quickly.
Very soon Laser Heads, Double Extrusion and Direct Drive will be developed.

In this development, I wanted to provide everyone the opportunity to have a DIY 3D printer in a box,
with the list of the best ingrediant cheaply that I have tried over time (Electronics, Extruder,
Hotend) but also to provide detailed plans and nomenclatures. Plus, you will also find the DXF Plate
Cutting Files and the names of the suppliers who can perform the service, at the best cost I could
find.
I also wanted to provide some assembly plans allowing the Novice to be able to launch this without
any doubt in the assembly of the chassis.

Profile frame 3030 B-Type Slot 8
2020 Profile B-Type Slot 6 Bed Support
DIBOND front and side closure plate brushed aluminum
A chassis kit will soon be available on the website http://www.Systeal.com
Dibond plates can be ordered at https://gen3d.fr/

All plans and files are provided free of charge, however I formally forbid the resumption of my
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

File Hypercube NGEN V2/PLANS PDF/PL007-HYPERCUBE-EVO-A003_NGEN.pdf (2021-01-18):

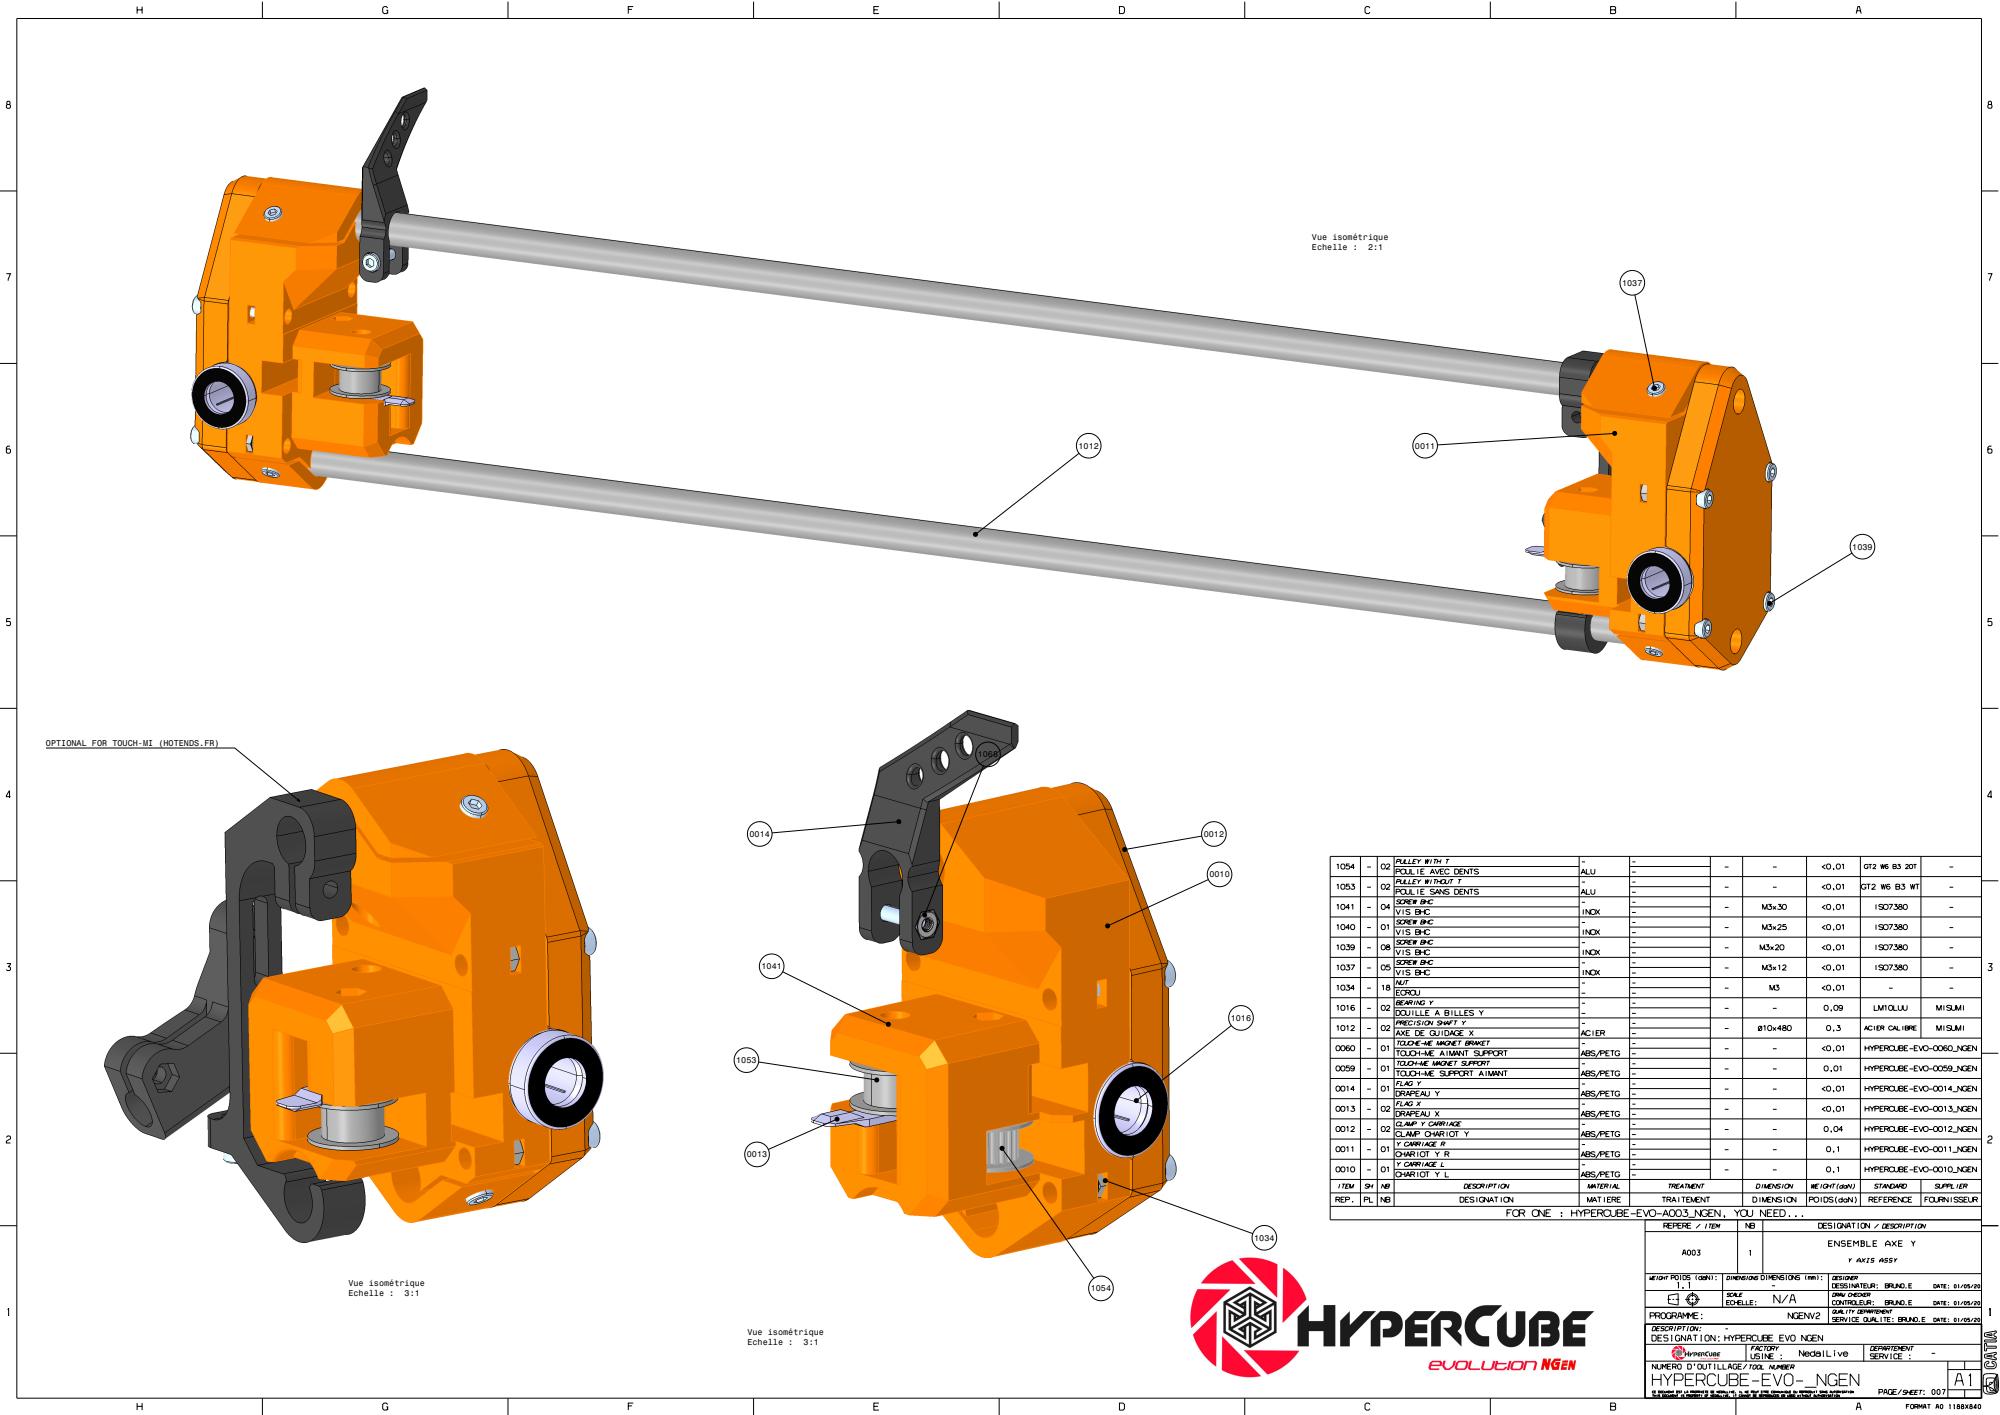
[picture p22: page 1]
Vue isométrique Echelle : 2:1; Vue isométrique Echelle : 3:1

OPTIONAL FOR TOUCH-MI (HOTENDS.FR)

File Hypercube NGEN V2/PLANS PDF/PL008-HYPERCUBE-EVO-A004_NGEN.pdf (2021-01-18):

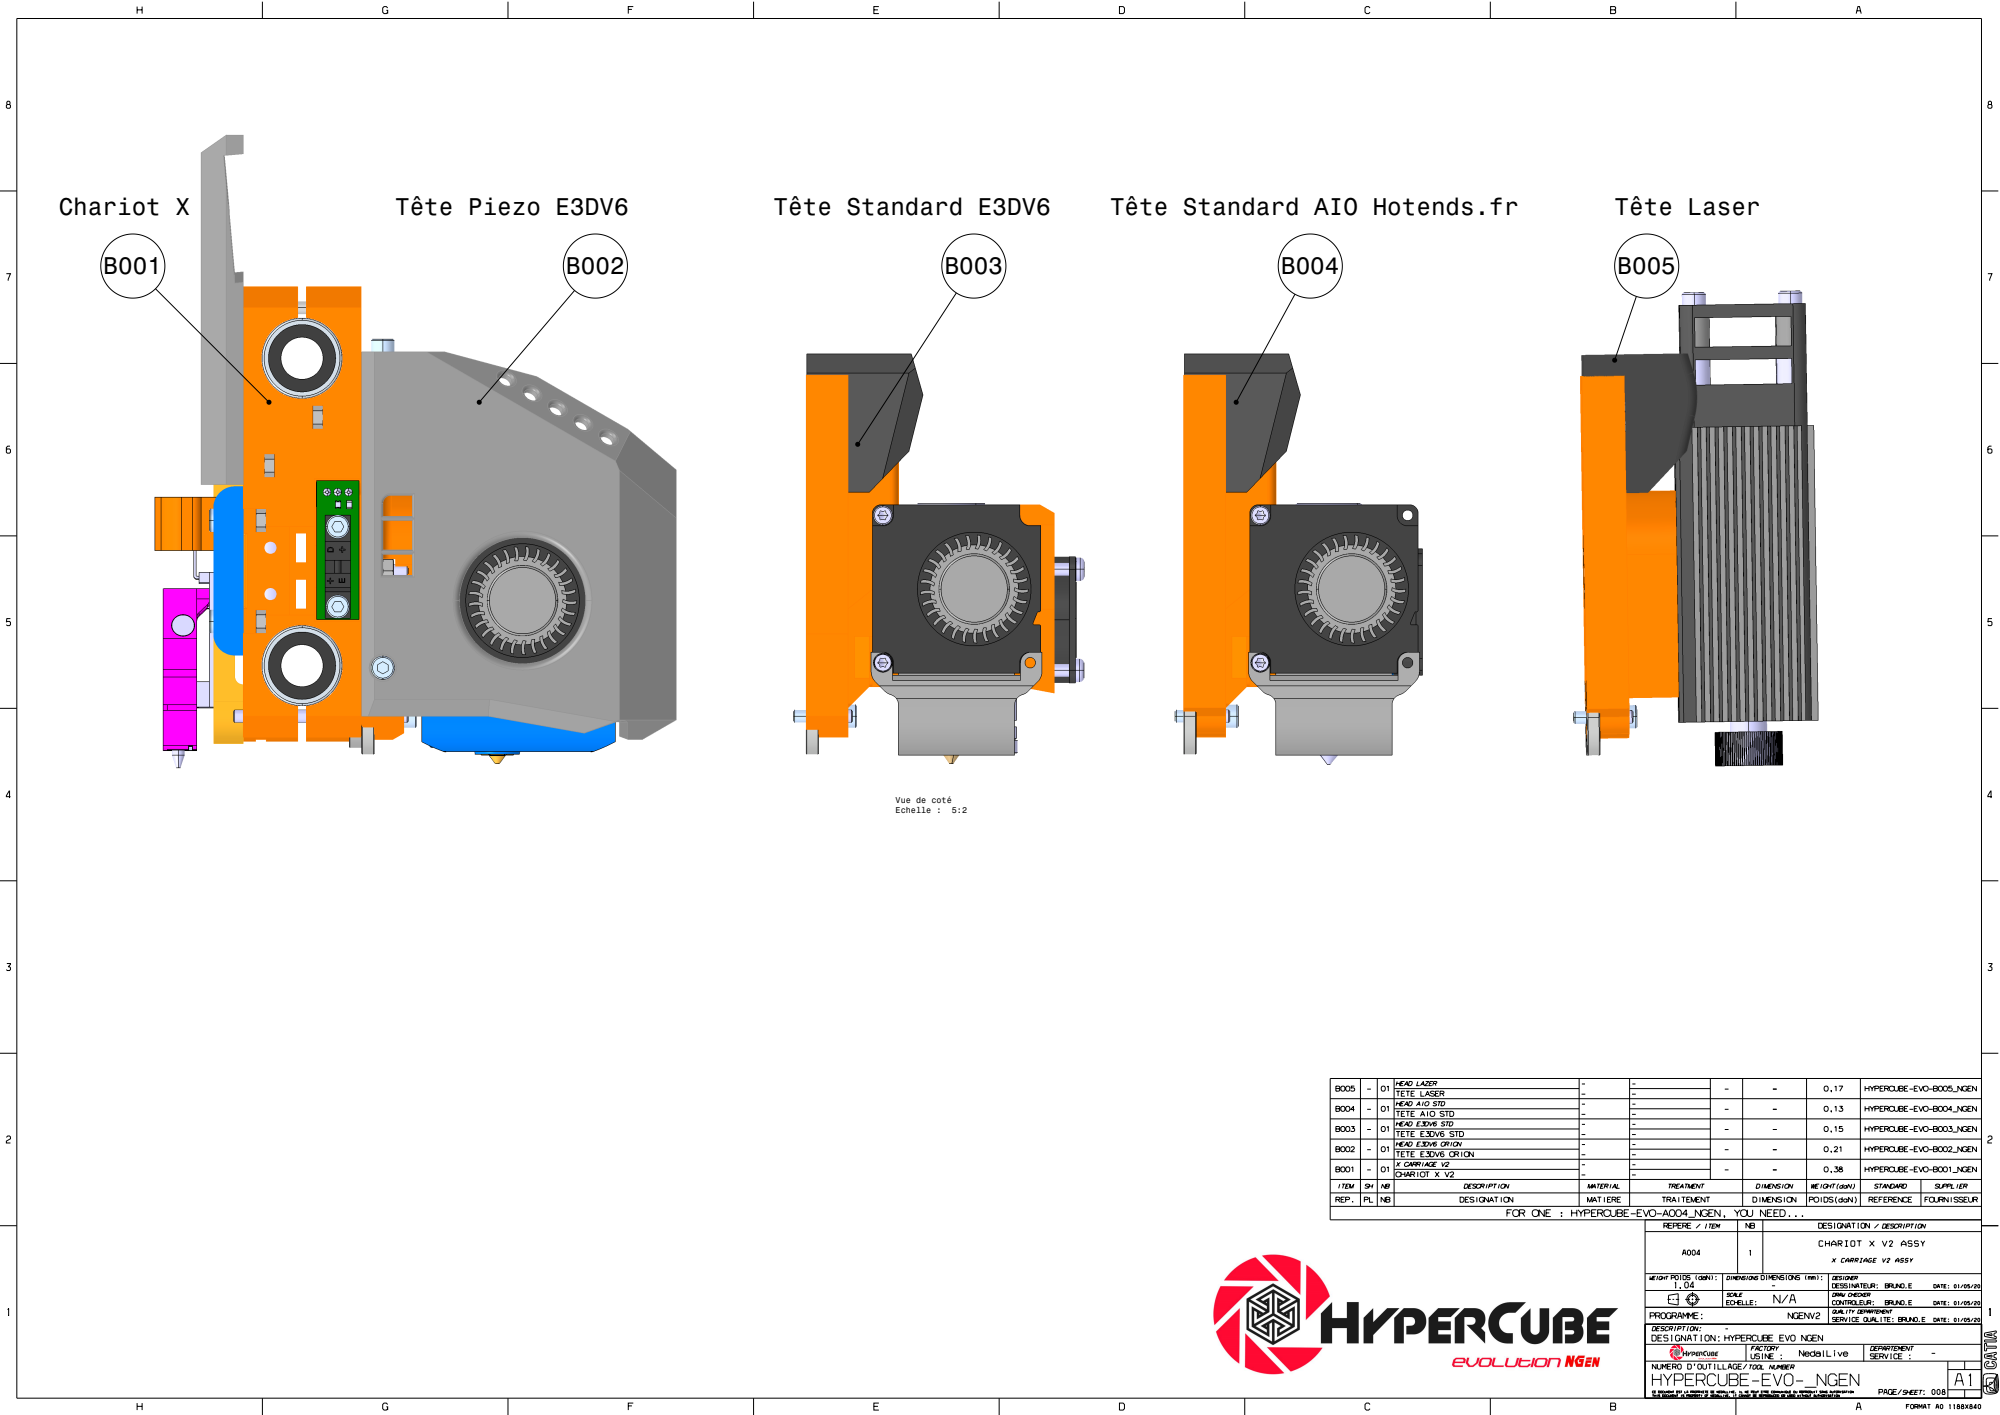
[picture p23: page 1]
Chariot X; Tête Piezo E3DV6; Tête Standard E3DV6; Tête Standard AIO Hotends.fr; Tête Laser

Vue de coté
Echelle : 5:2

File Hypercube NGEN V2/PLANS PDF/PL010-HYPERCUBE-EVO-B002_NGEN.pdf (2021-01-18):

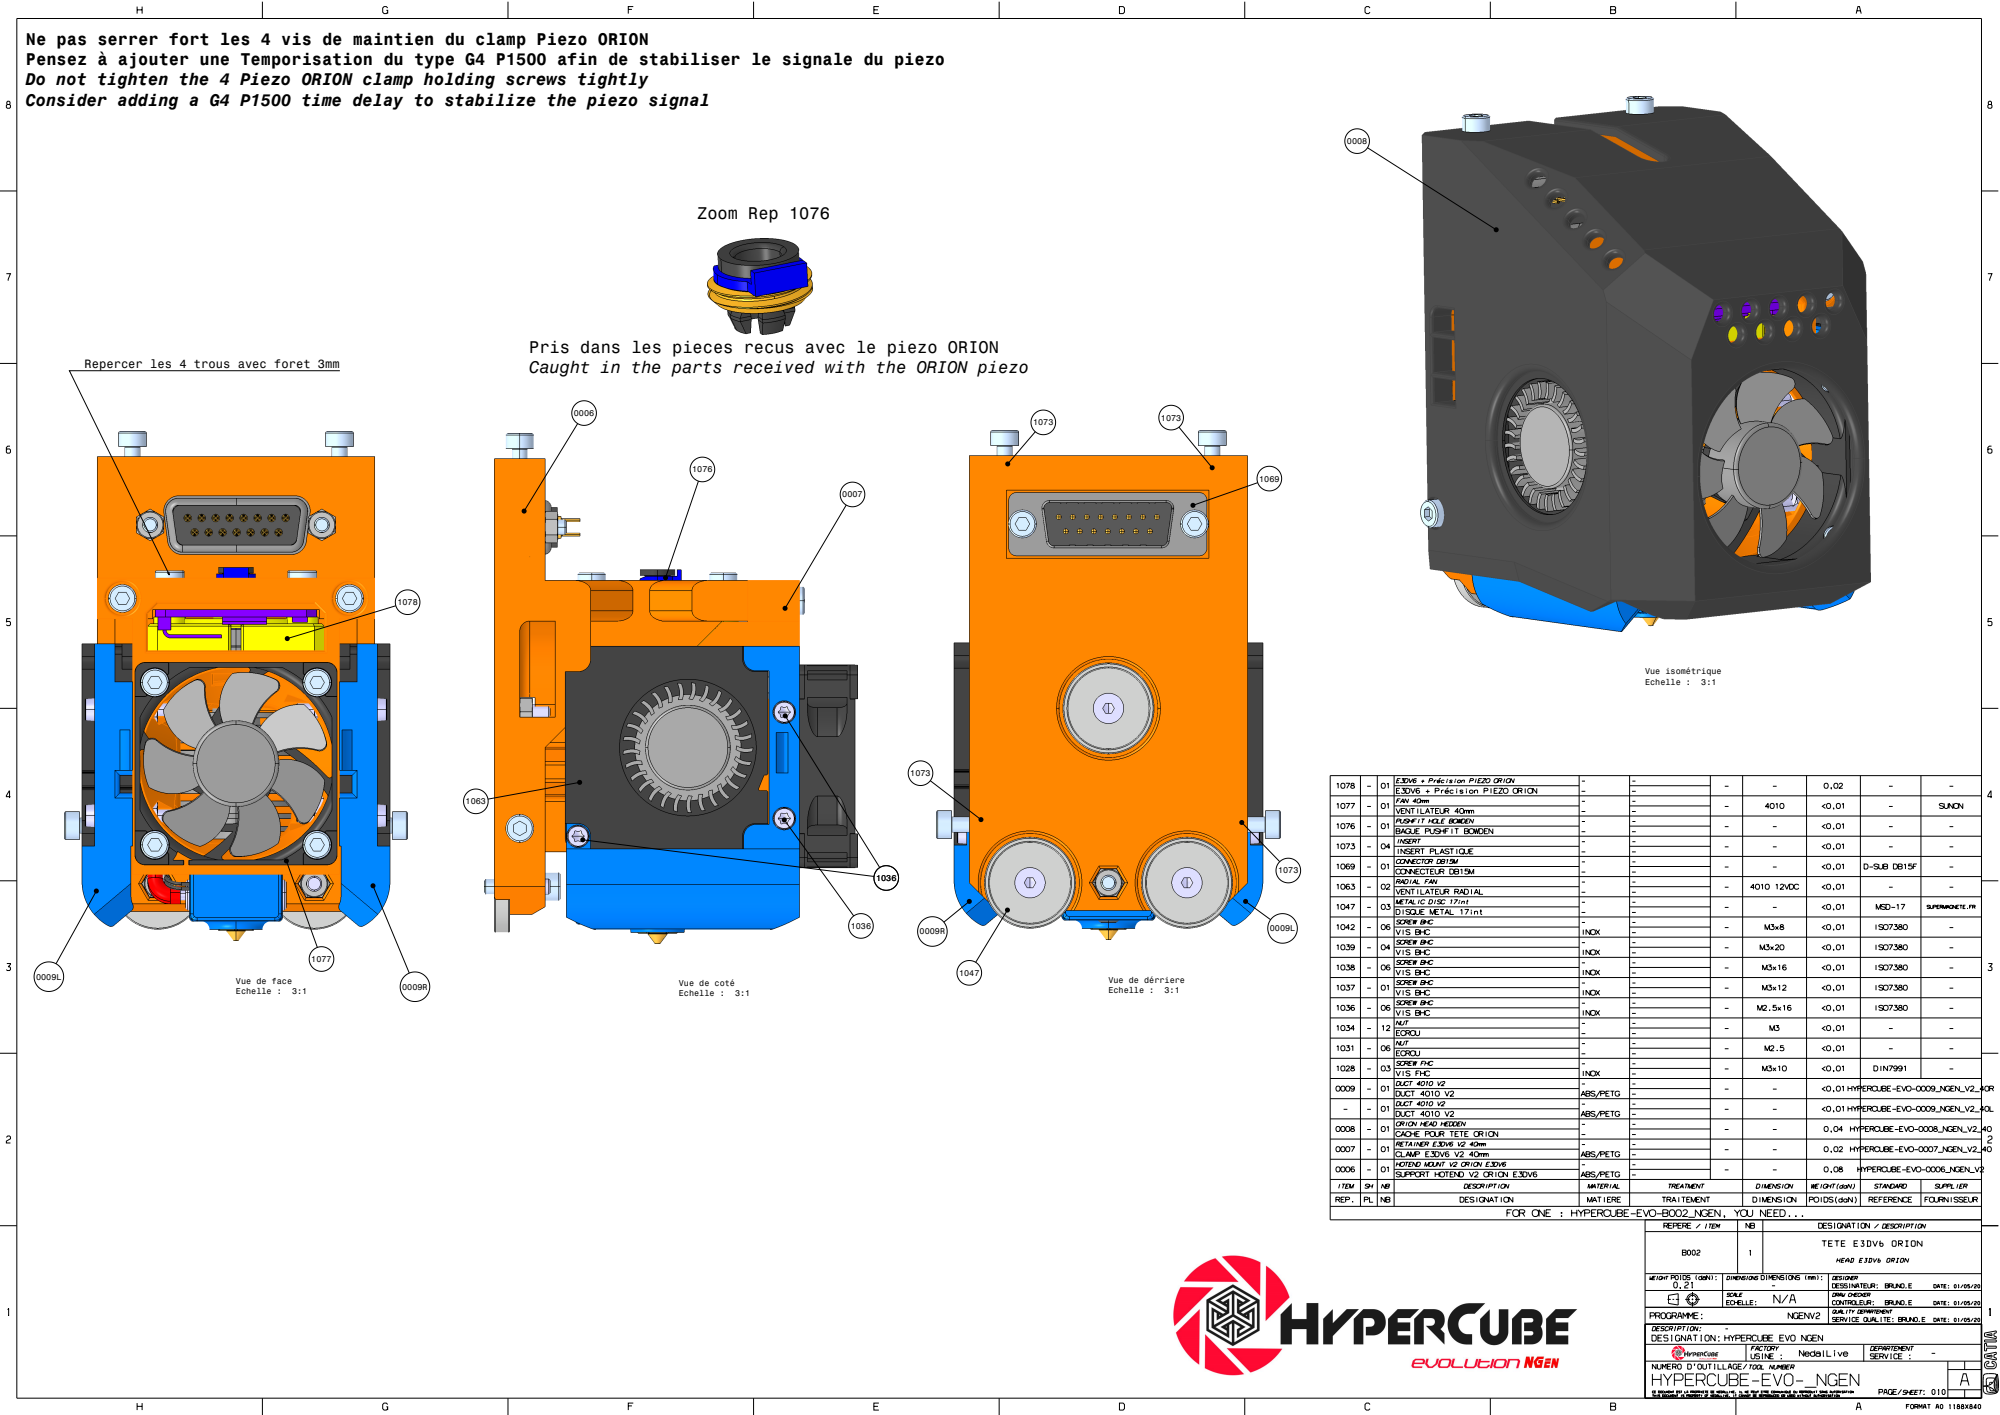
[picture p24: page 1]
Vue isométrique Echelle : 3:1; Zoom Rep 1076

Ne pas serrer fort les 4 vis de maintien du clamp Piezo ORION
Pensez à ajouter une Temporisation du type G4 P1500 afin de stabiliser le signale du piezo
Do not tighten the 4 Piezo ORION clamp holding screws tightly
Consider adding a G4 P1500 time delay to stabilize the piezo signal

Pris dans les pieces recus avec le piezo ORION
Caught in the parts received with the ORION piezo

Repercer les 4 trous avec foret 3mm

Vue de face
Echelle : 3:1

Vue de dérriere

Vue de coté

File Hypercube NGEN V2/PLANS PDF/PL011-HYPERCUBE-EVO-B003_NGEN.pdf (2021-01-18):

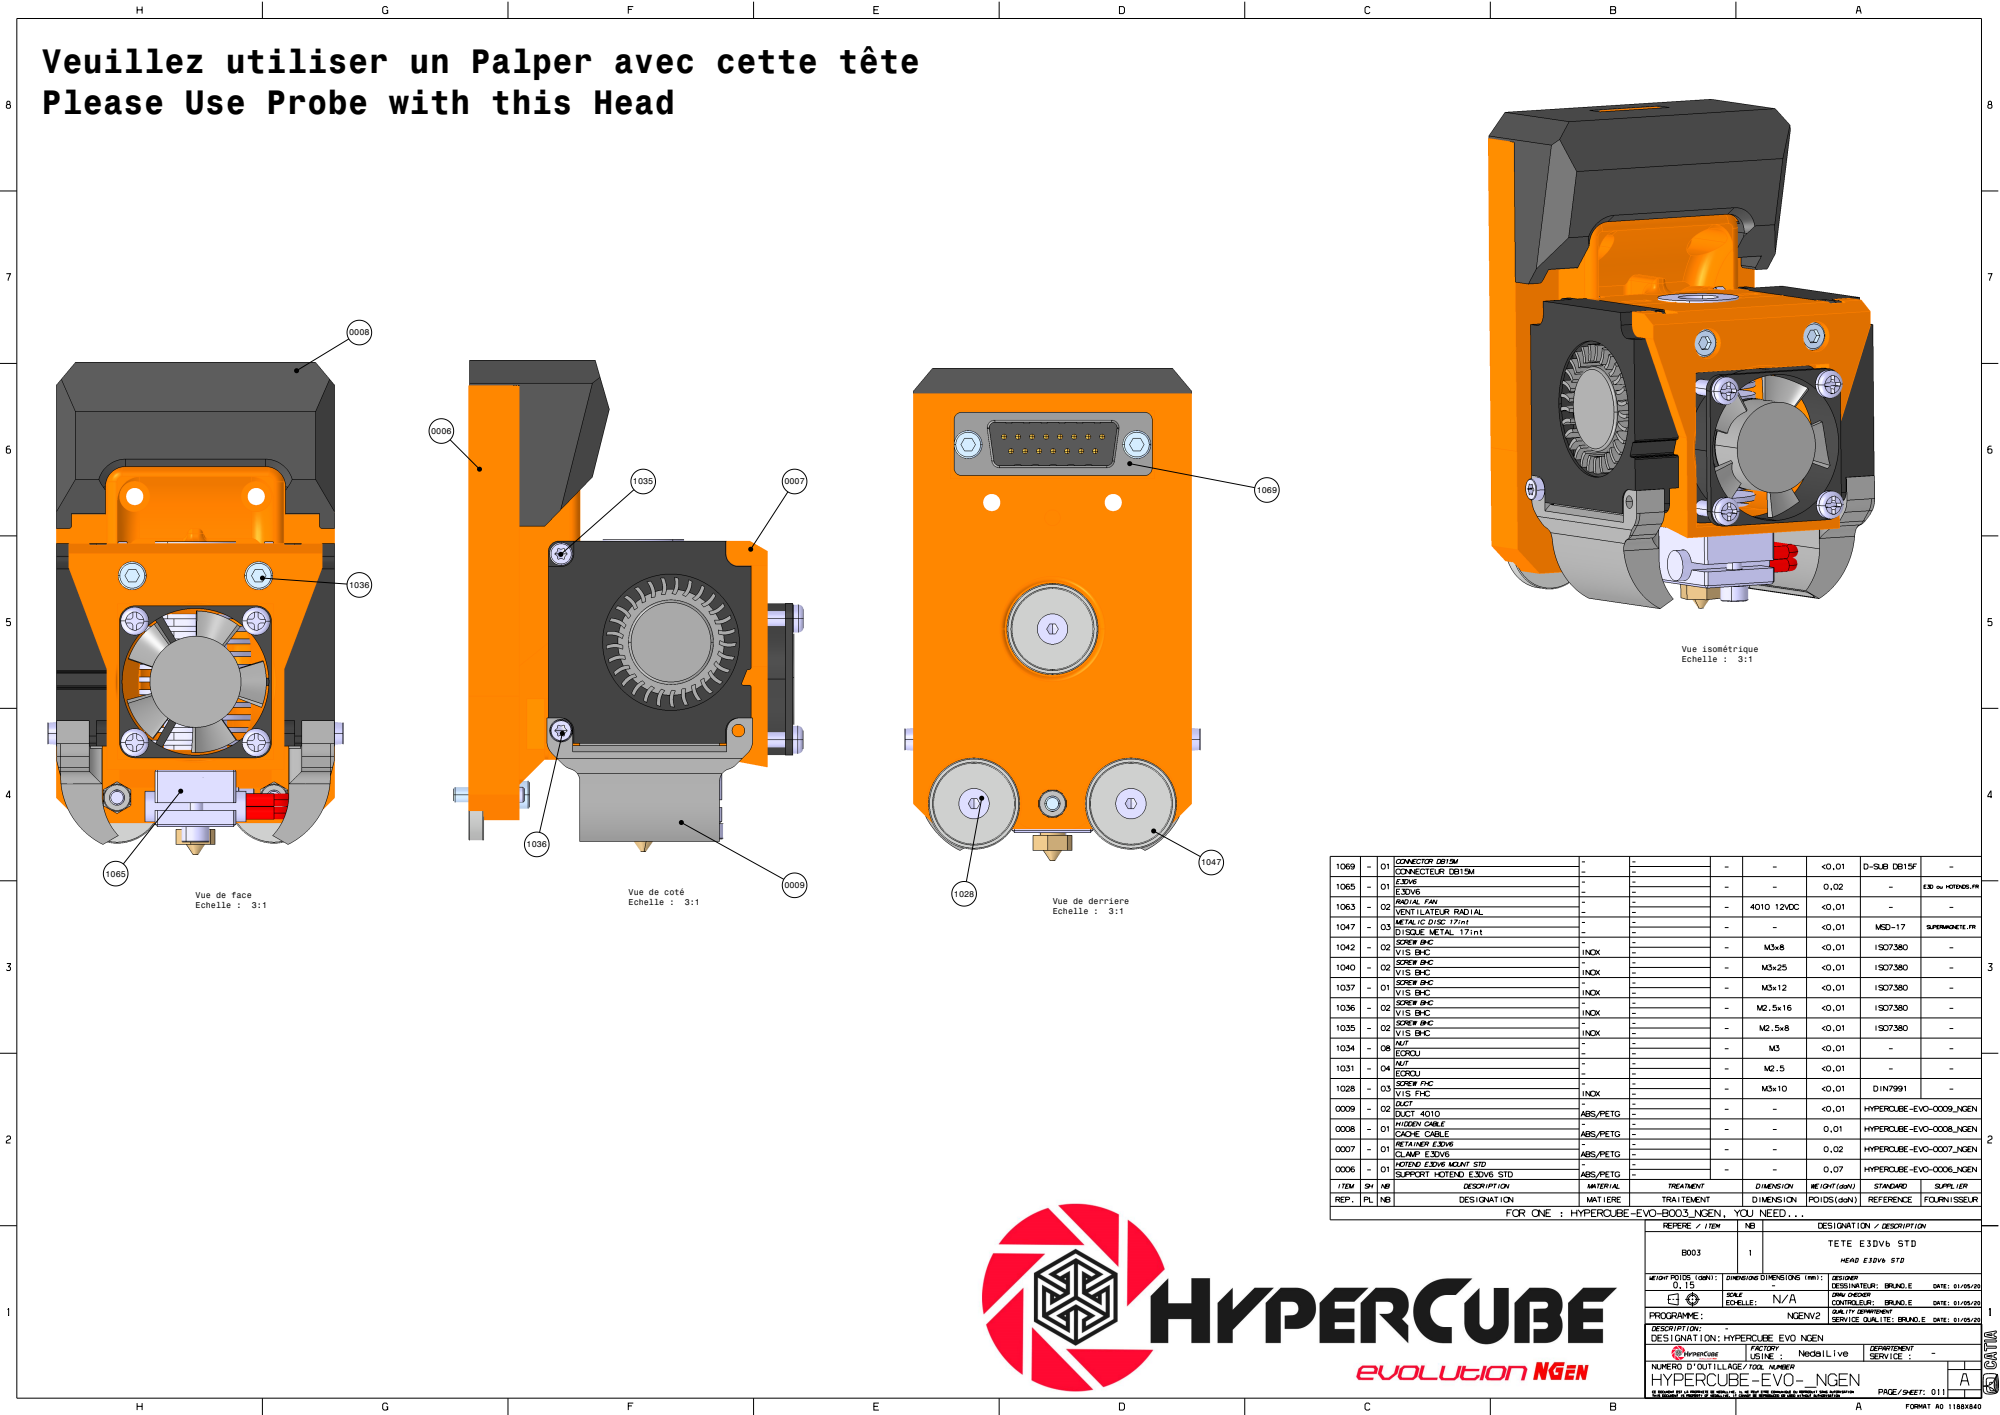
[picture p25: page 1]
Vue isométrique Echelle : 3:1

Veuillez utiliser un Palper avec cette tête
Please Use Probe with this Head

Vue de face
Echelle : 3:1

Vue de coté

Vue de derriere

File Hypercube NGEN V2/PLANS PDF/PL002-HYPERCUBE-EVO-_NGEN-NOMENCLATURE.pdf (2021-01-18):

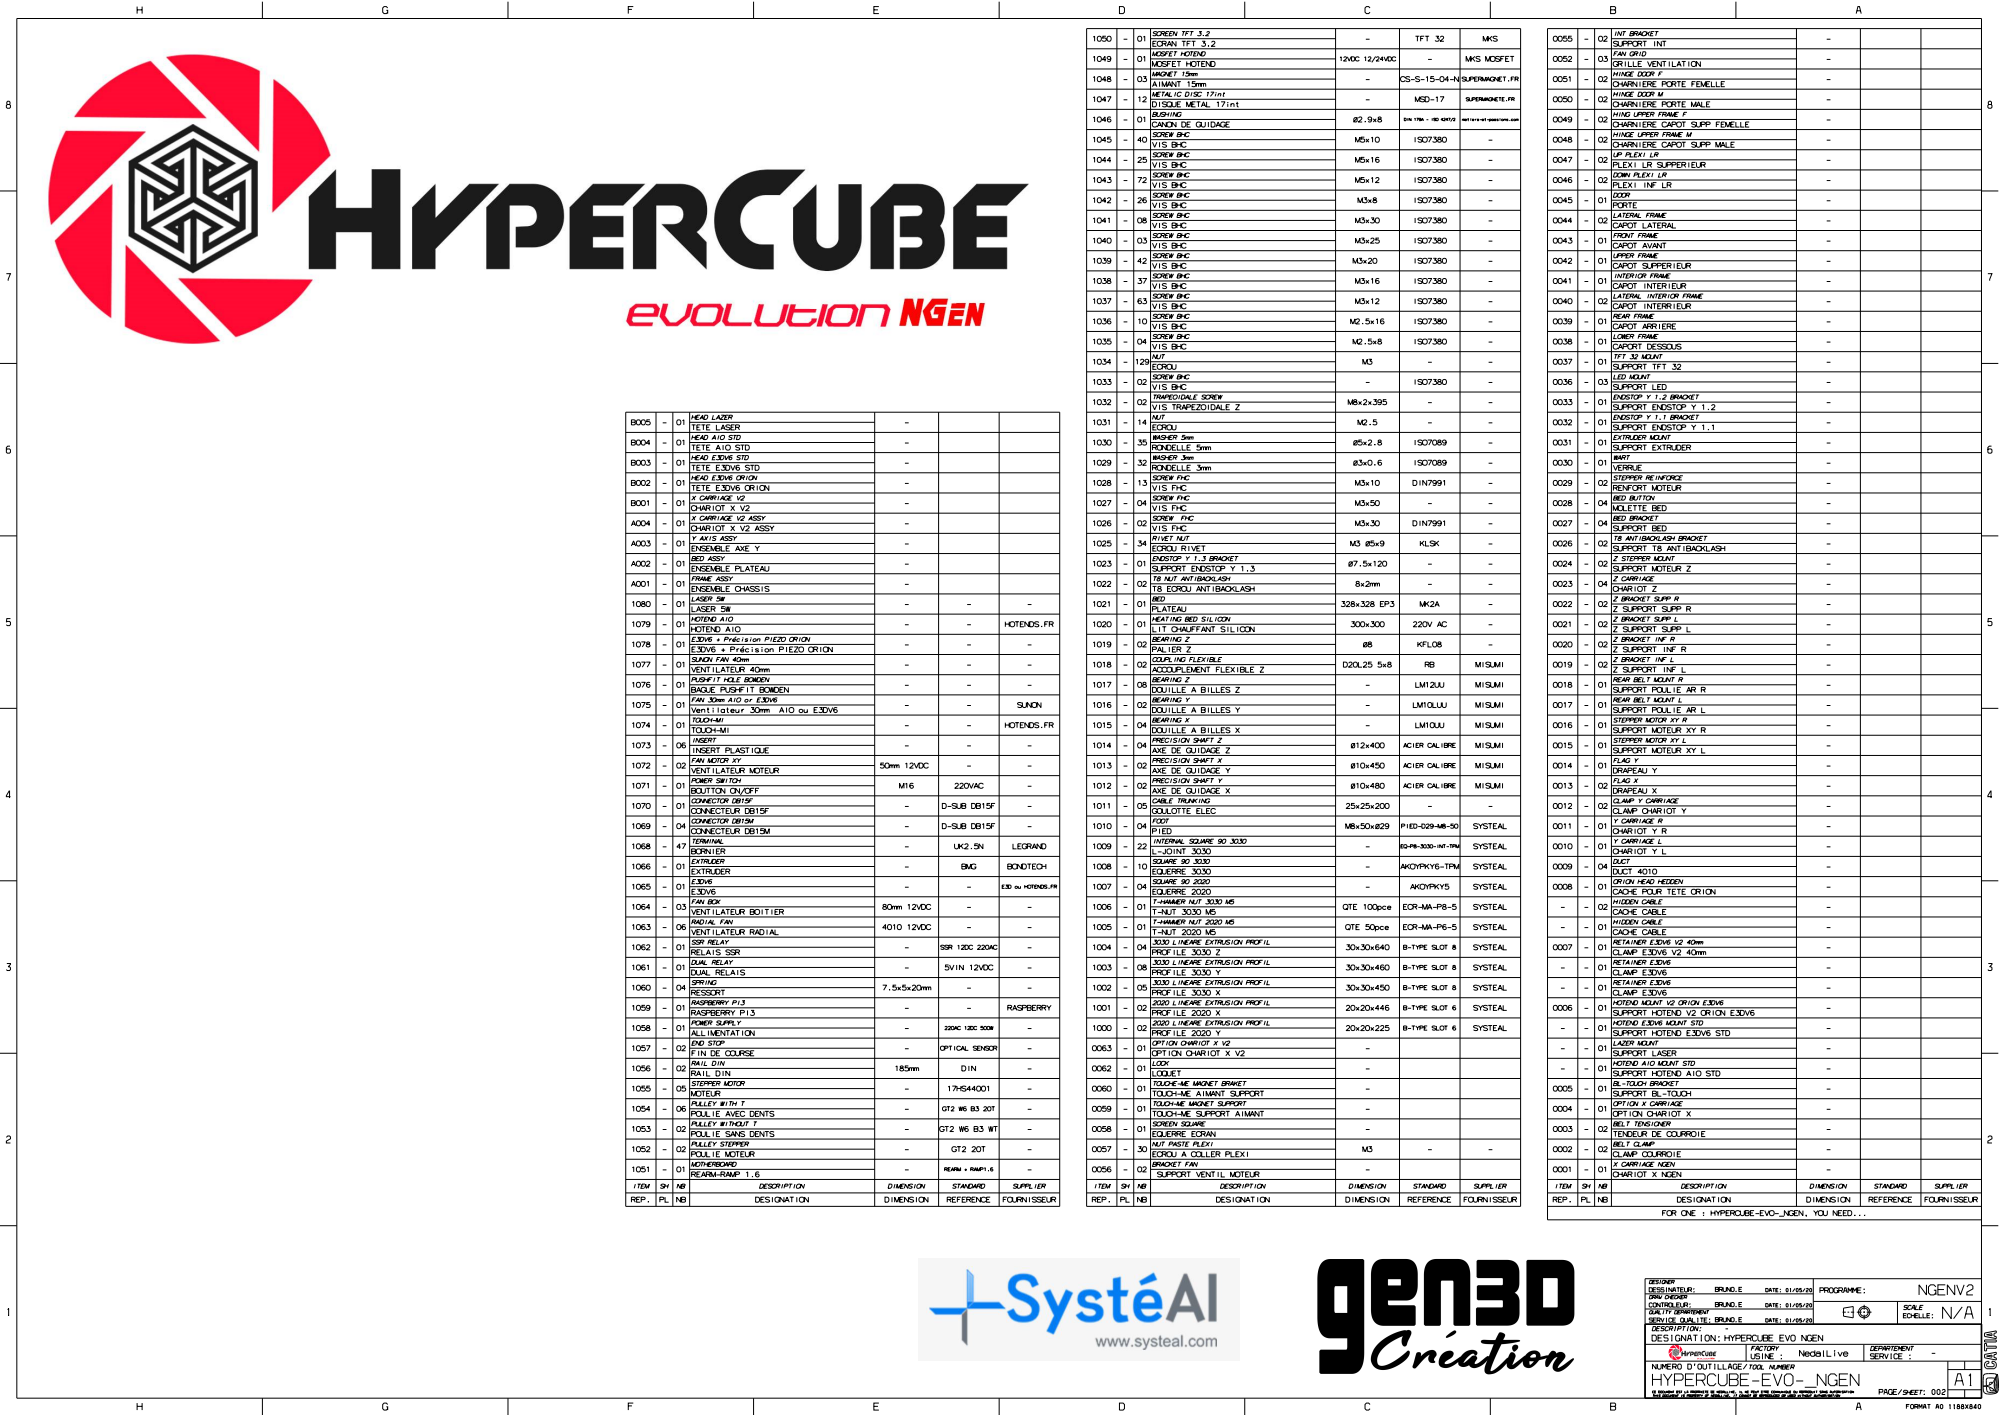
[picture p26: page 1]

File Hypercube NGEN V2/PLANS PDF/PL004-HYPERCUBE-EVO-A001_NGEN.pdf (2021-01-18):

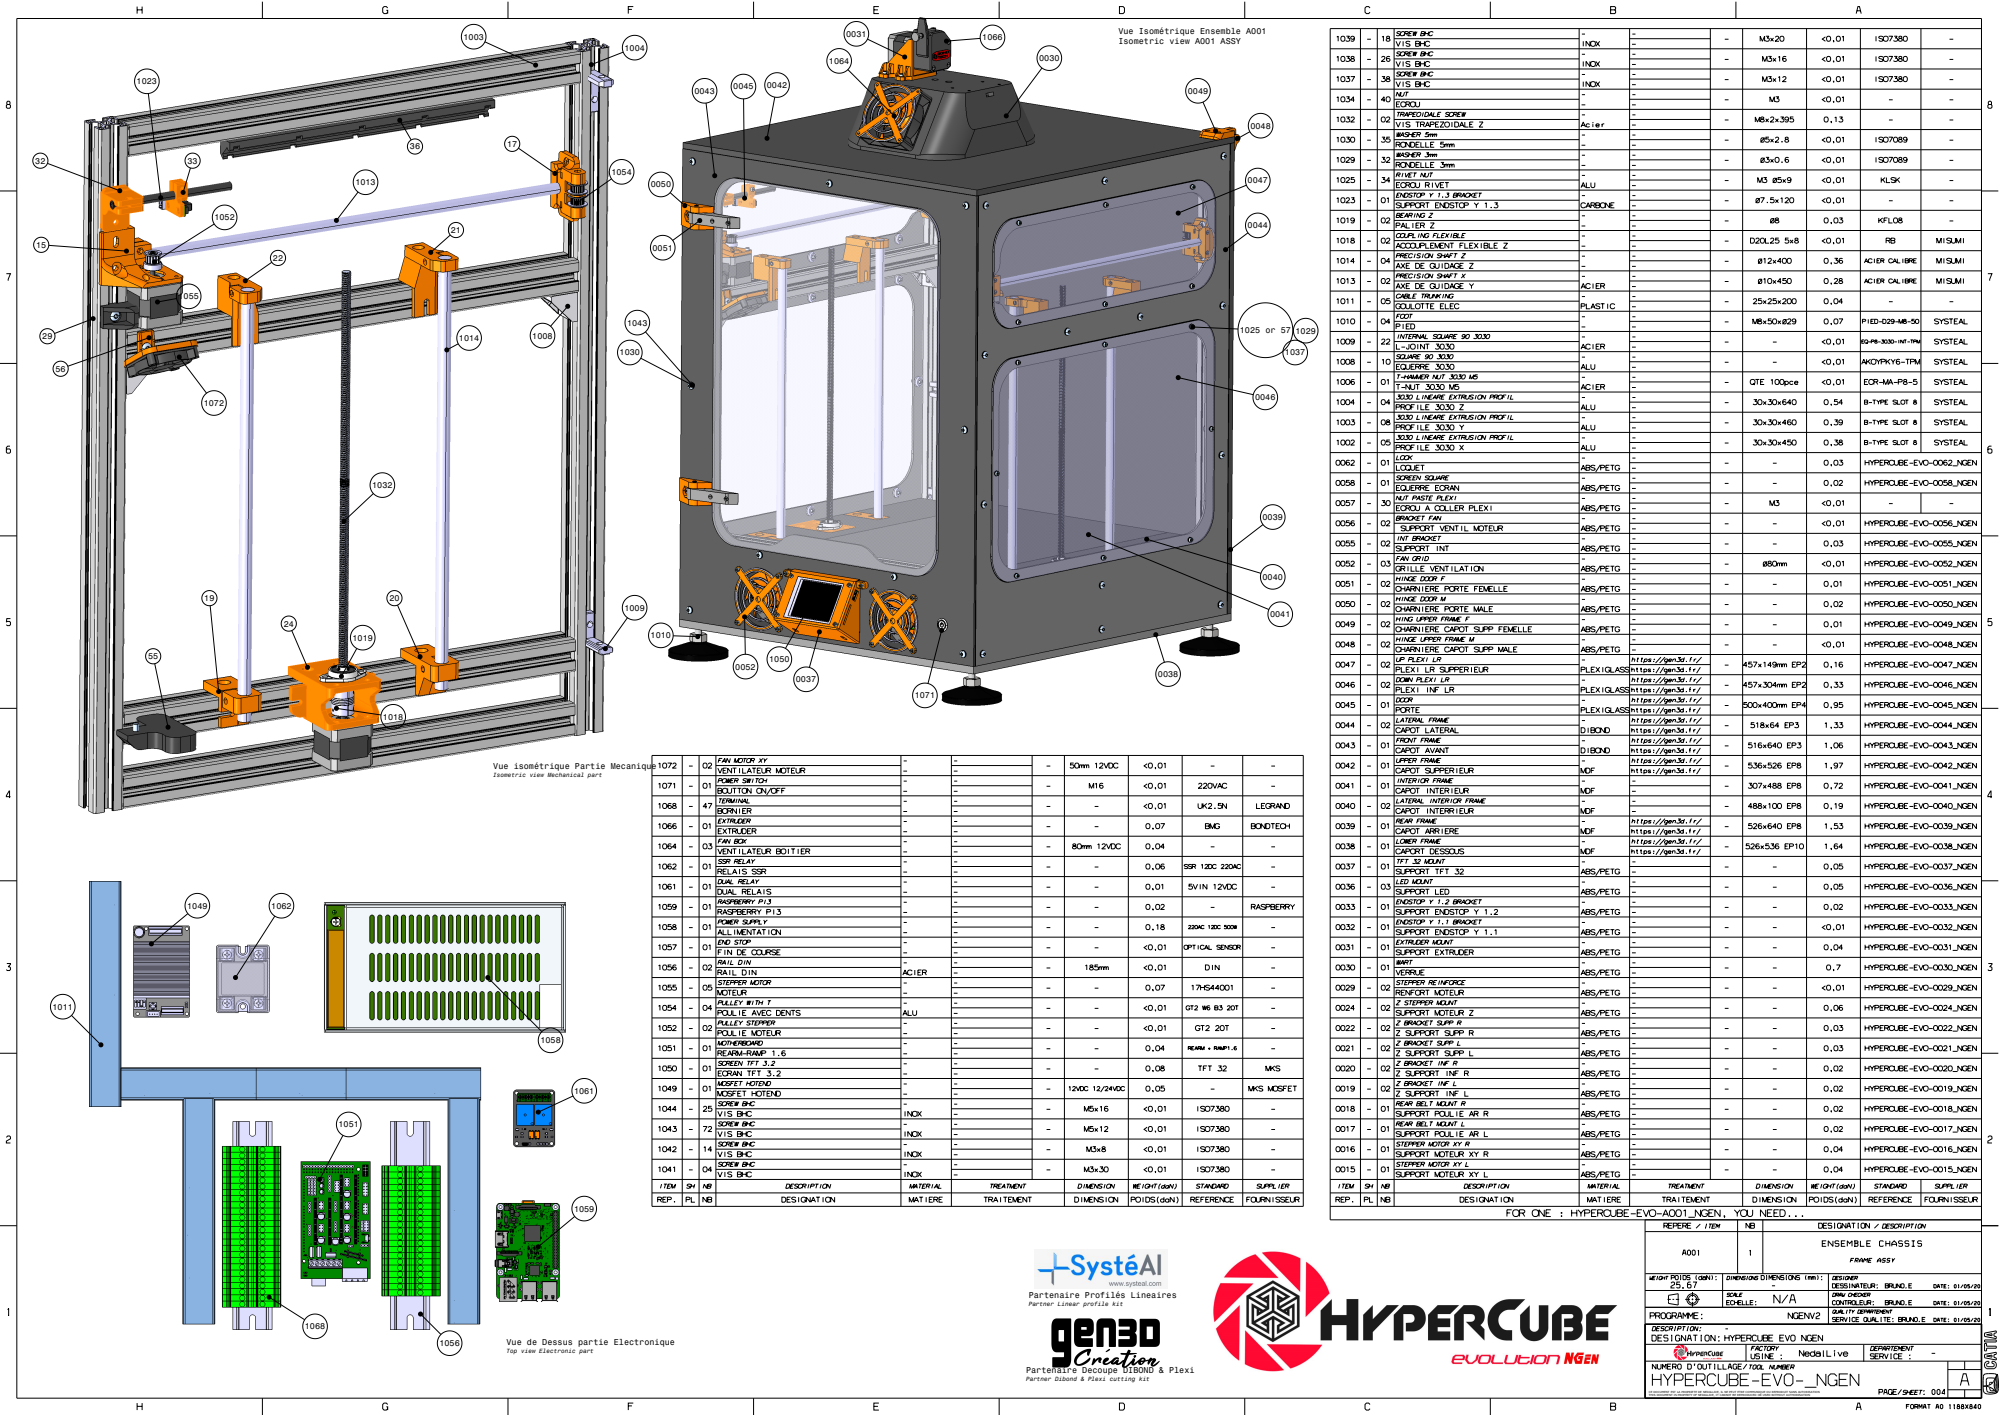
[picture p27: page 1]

Vue Isométrique Ensemble A001
Isometric view A001 ASSY

Vue isométrique Partie Mecanique
Isometric view Mechanical part

Partenaire Profilés Lineaires
Partner Linear profile kit

Vue de Dessus partie Electronique
Top view Electronic part

Partenaire Decoupe DIBOND & Plexi
Partner Dibond & Plexi cutting kit

CE DOCUMENT EST LA PROPRIETE DE NEDALLIVE, IL NE PEUT ETRE COMMUNIQUE OU REPRODUIT SANS AUTORISATION
THIS DOCUMENT IS PROPERTY OF NEDALLIVE, IT CANNOT BE REPRODUCED OR USED WITHOUT AUTHORISATION

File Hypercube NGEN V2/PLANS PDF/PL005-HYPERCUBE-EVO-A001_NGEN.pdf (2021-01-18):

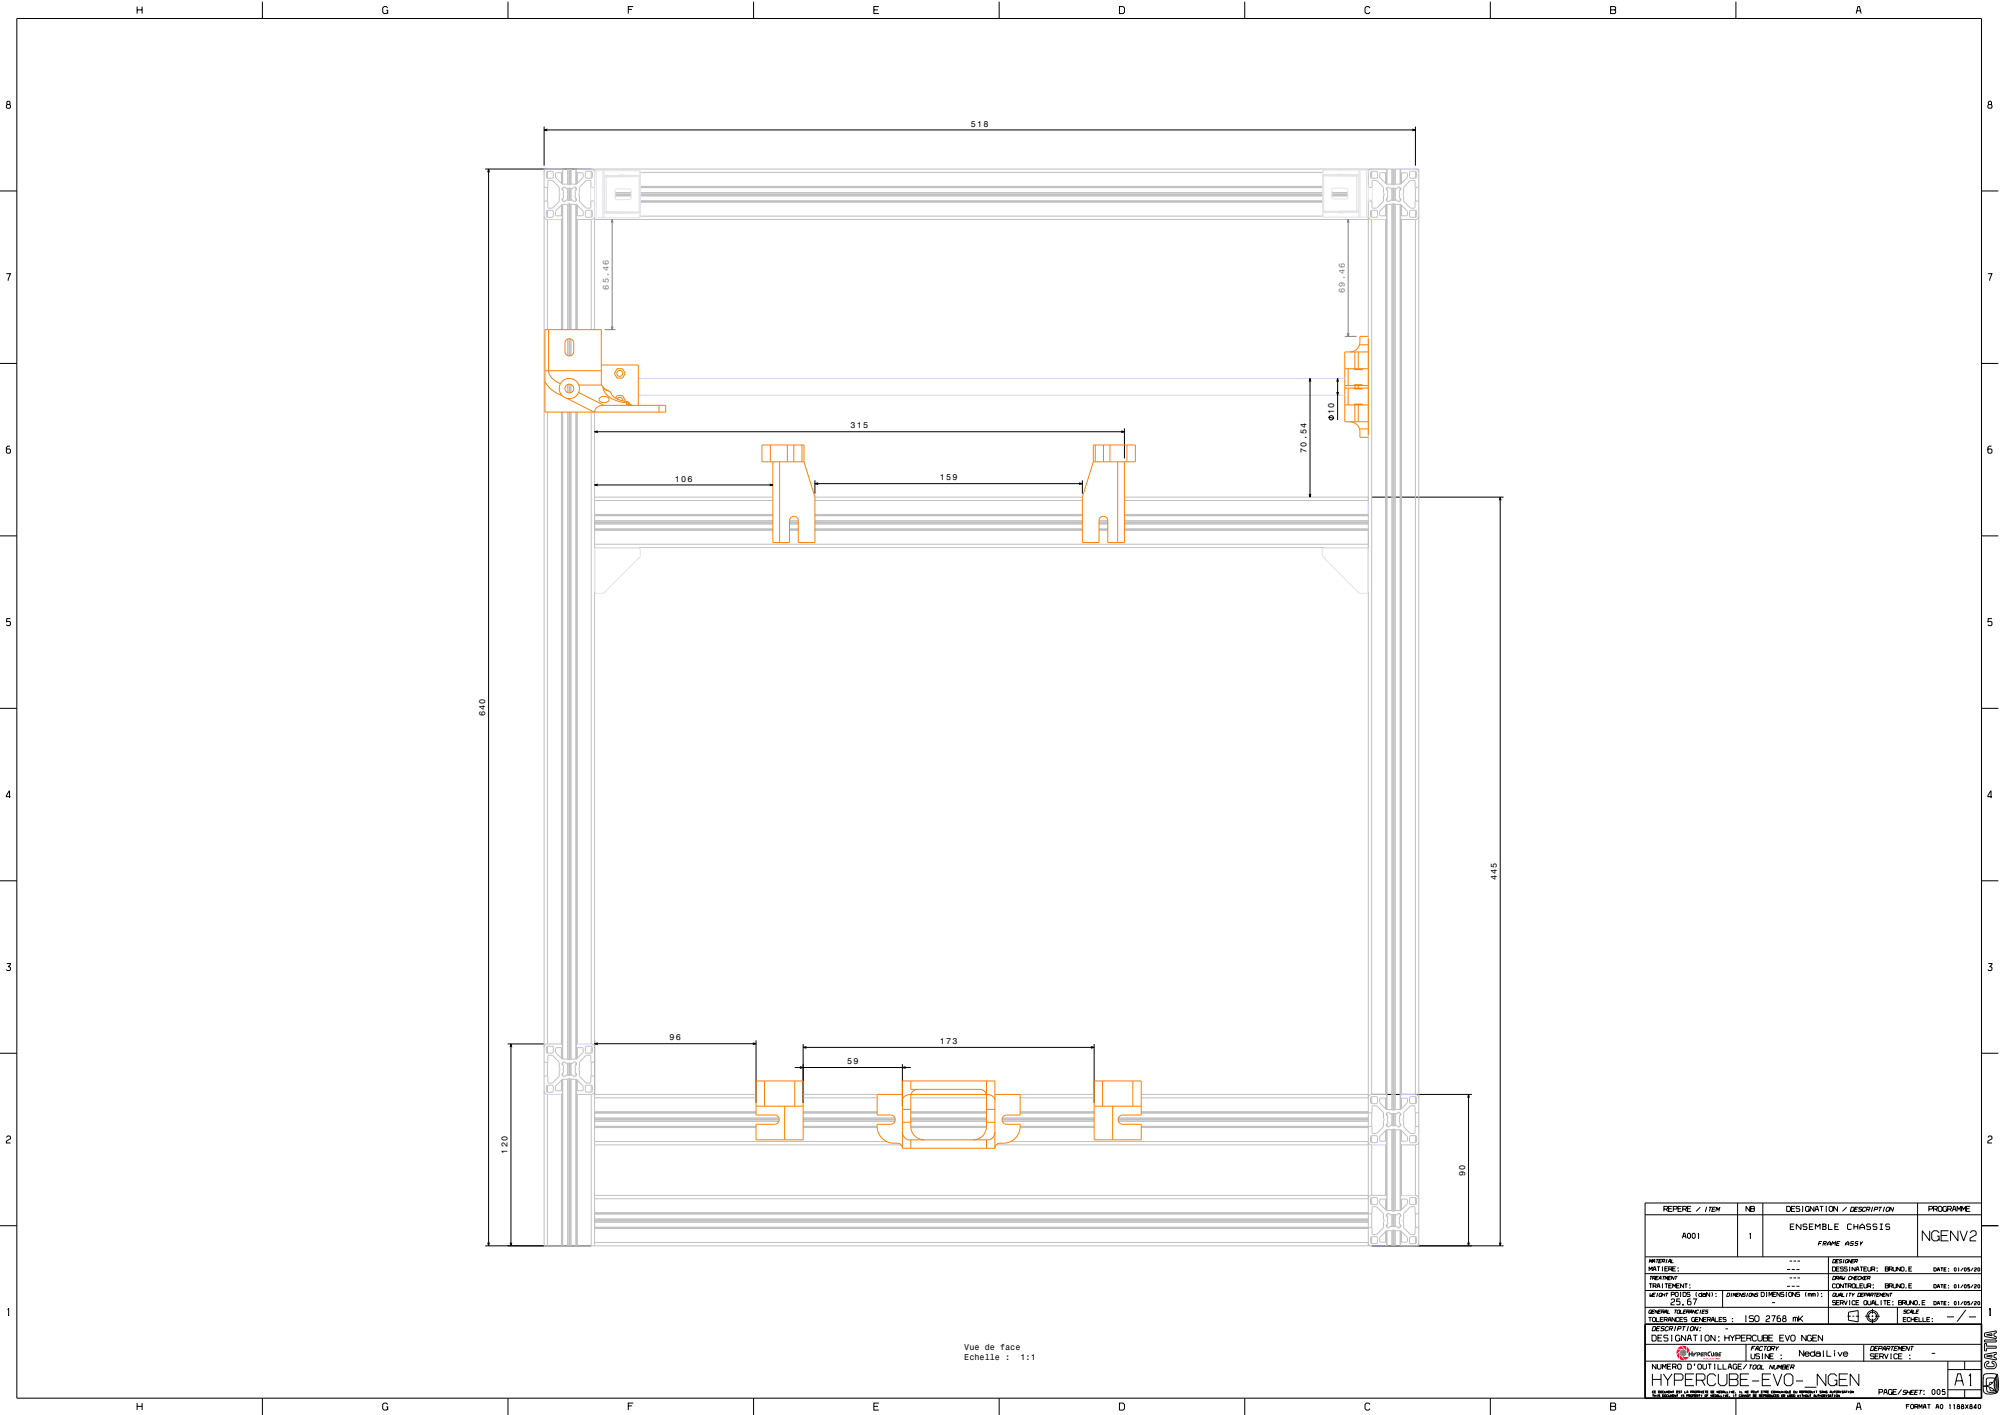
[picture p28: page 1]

Vue de face
Echelle : 1:1

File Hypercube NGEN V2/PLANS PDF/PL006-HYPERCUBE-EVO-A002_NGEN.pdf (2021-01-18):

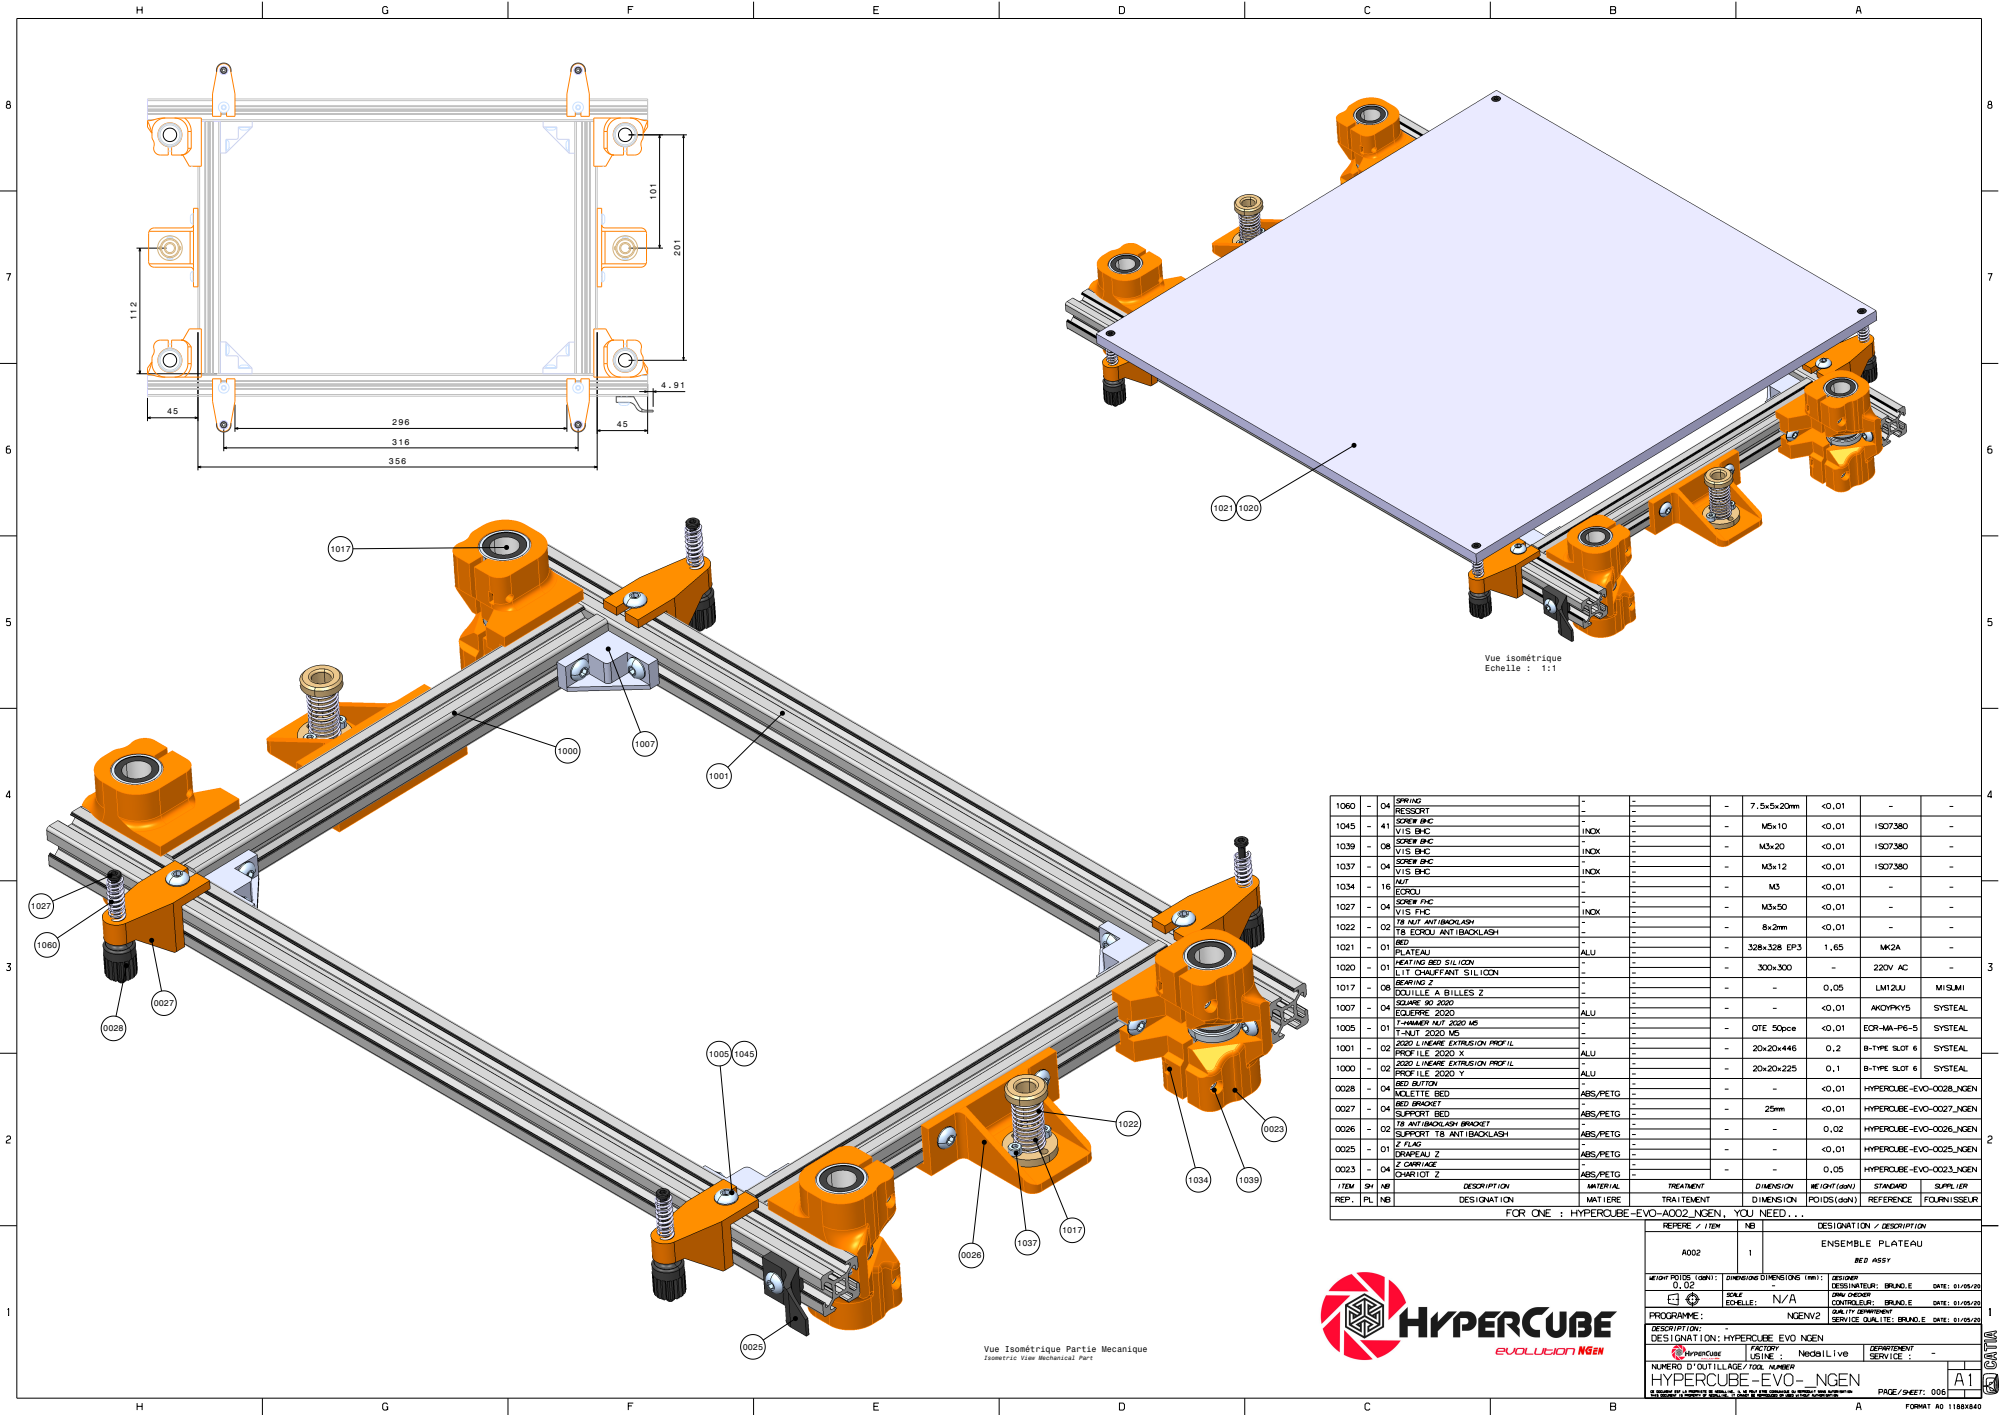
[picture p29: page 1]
Vue isométrique Echelle : 1:1

Vue Isométrique Partie Mecanique
Isometric View Mechanical Part

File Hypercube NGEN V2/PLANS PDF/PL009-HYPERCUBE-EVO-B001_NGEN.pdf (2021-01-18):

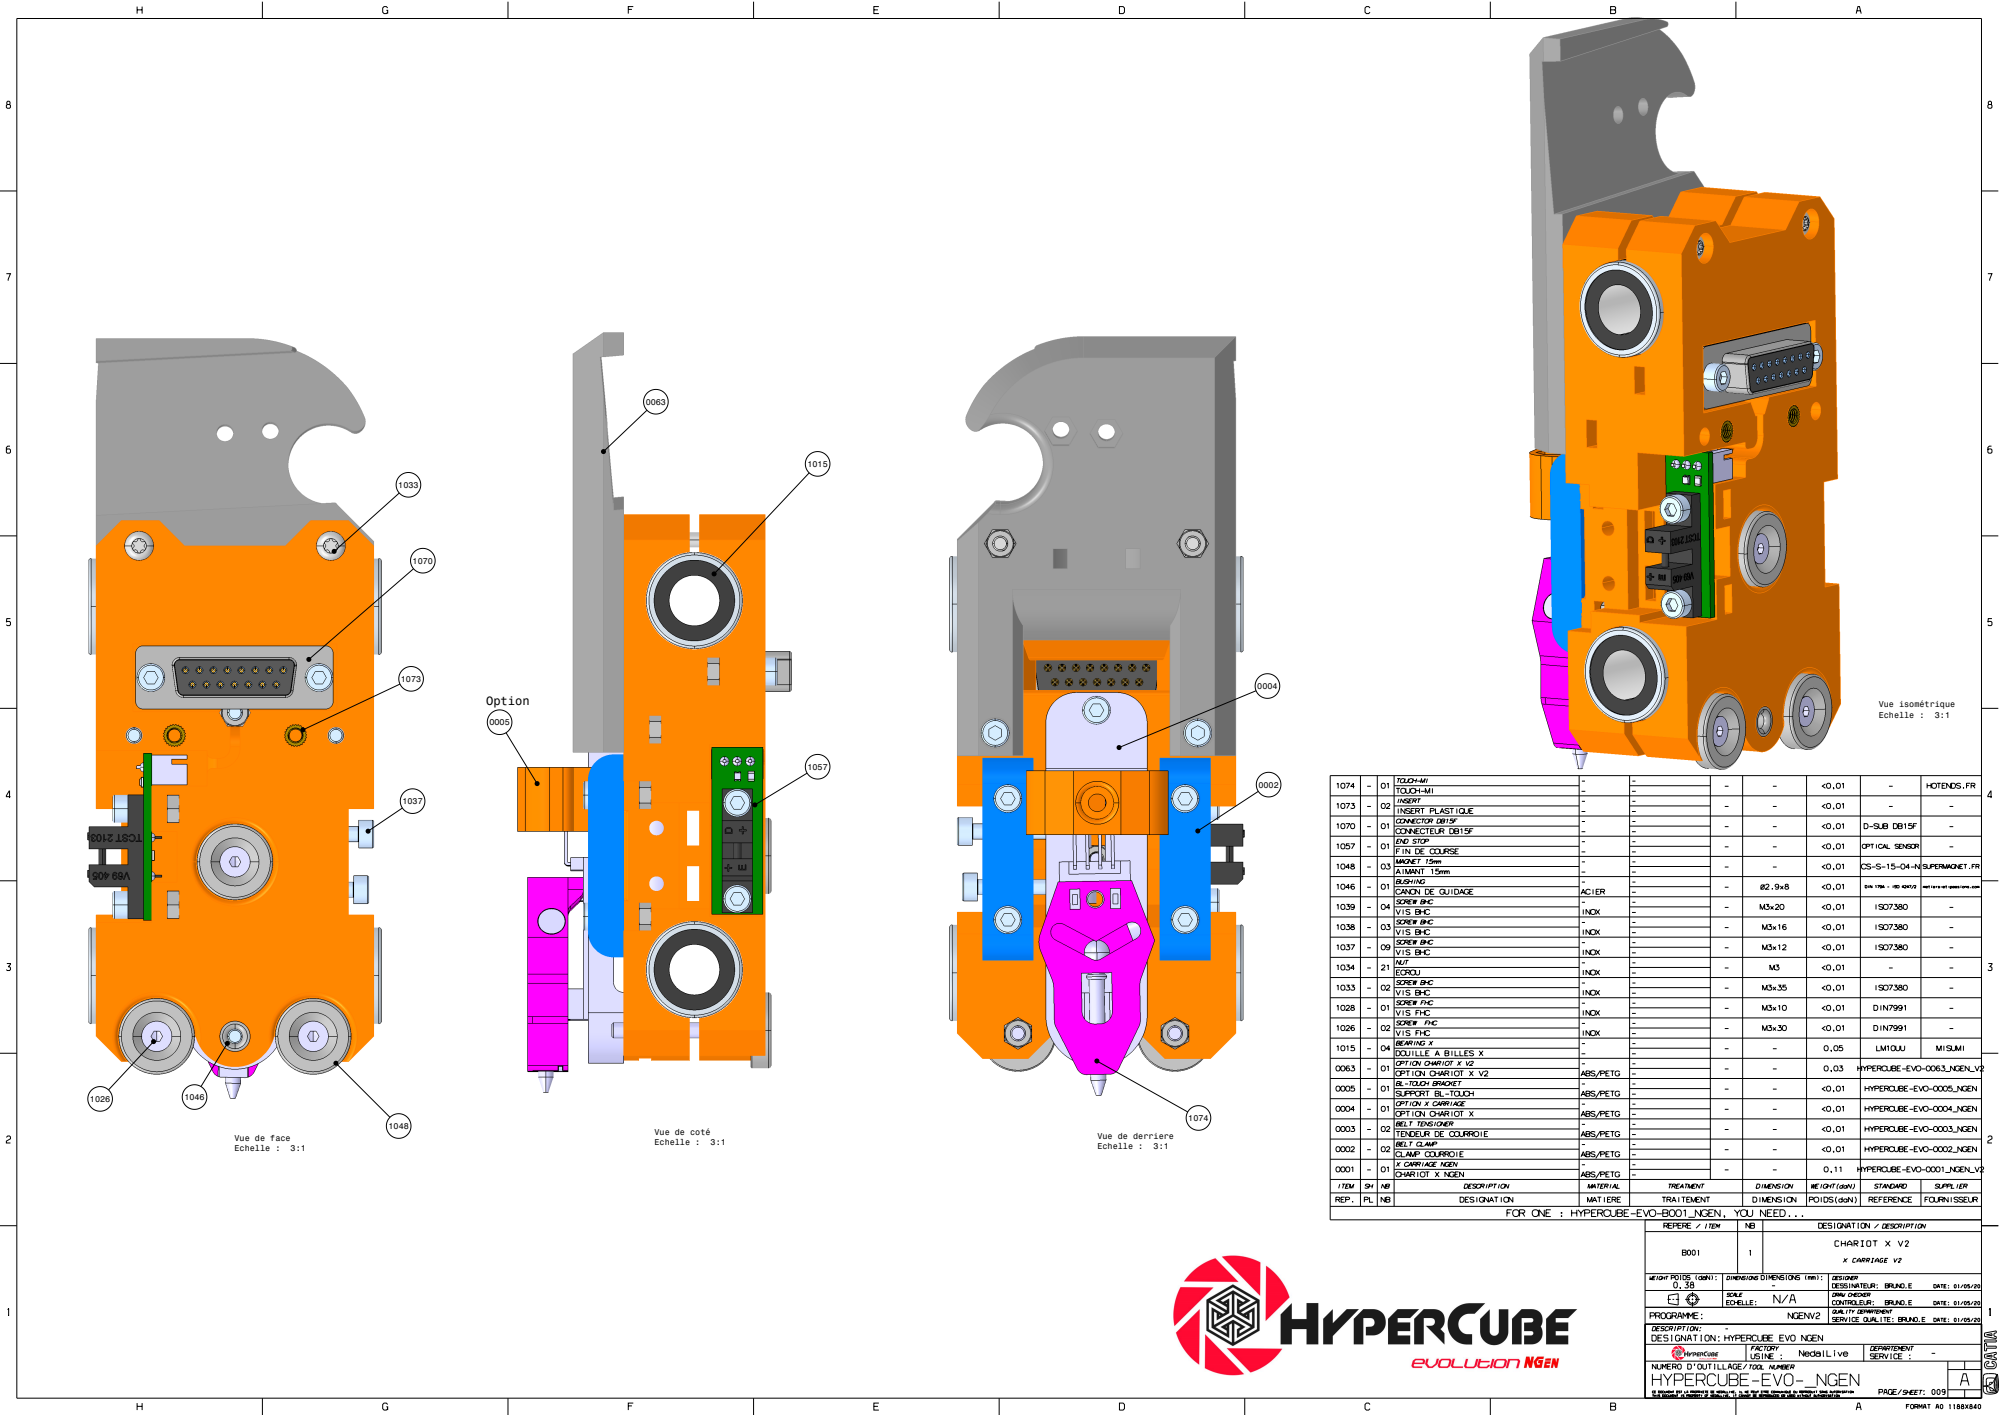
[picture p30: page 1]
Vue isométrique Echelle : 3:1

Vue de coté
Echelle : 3:1

Vue de derriere

Vue de face

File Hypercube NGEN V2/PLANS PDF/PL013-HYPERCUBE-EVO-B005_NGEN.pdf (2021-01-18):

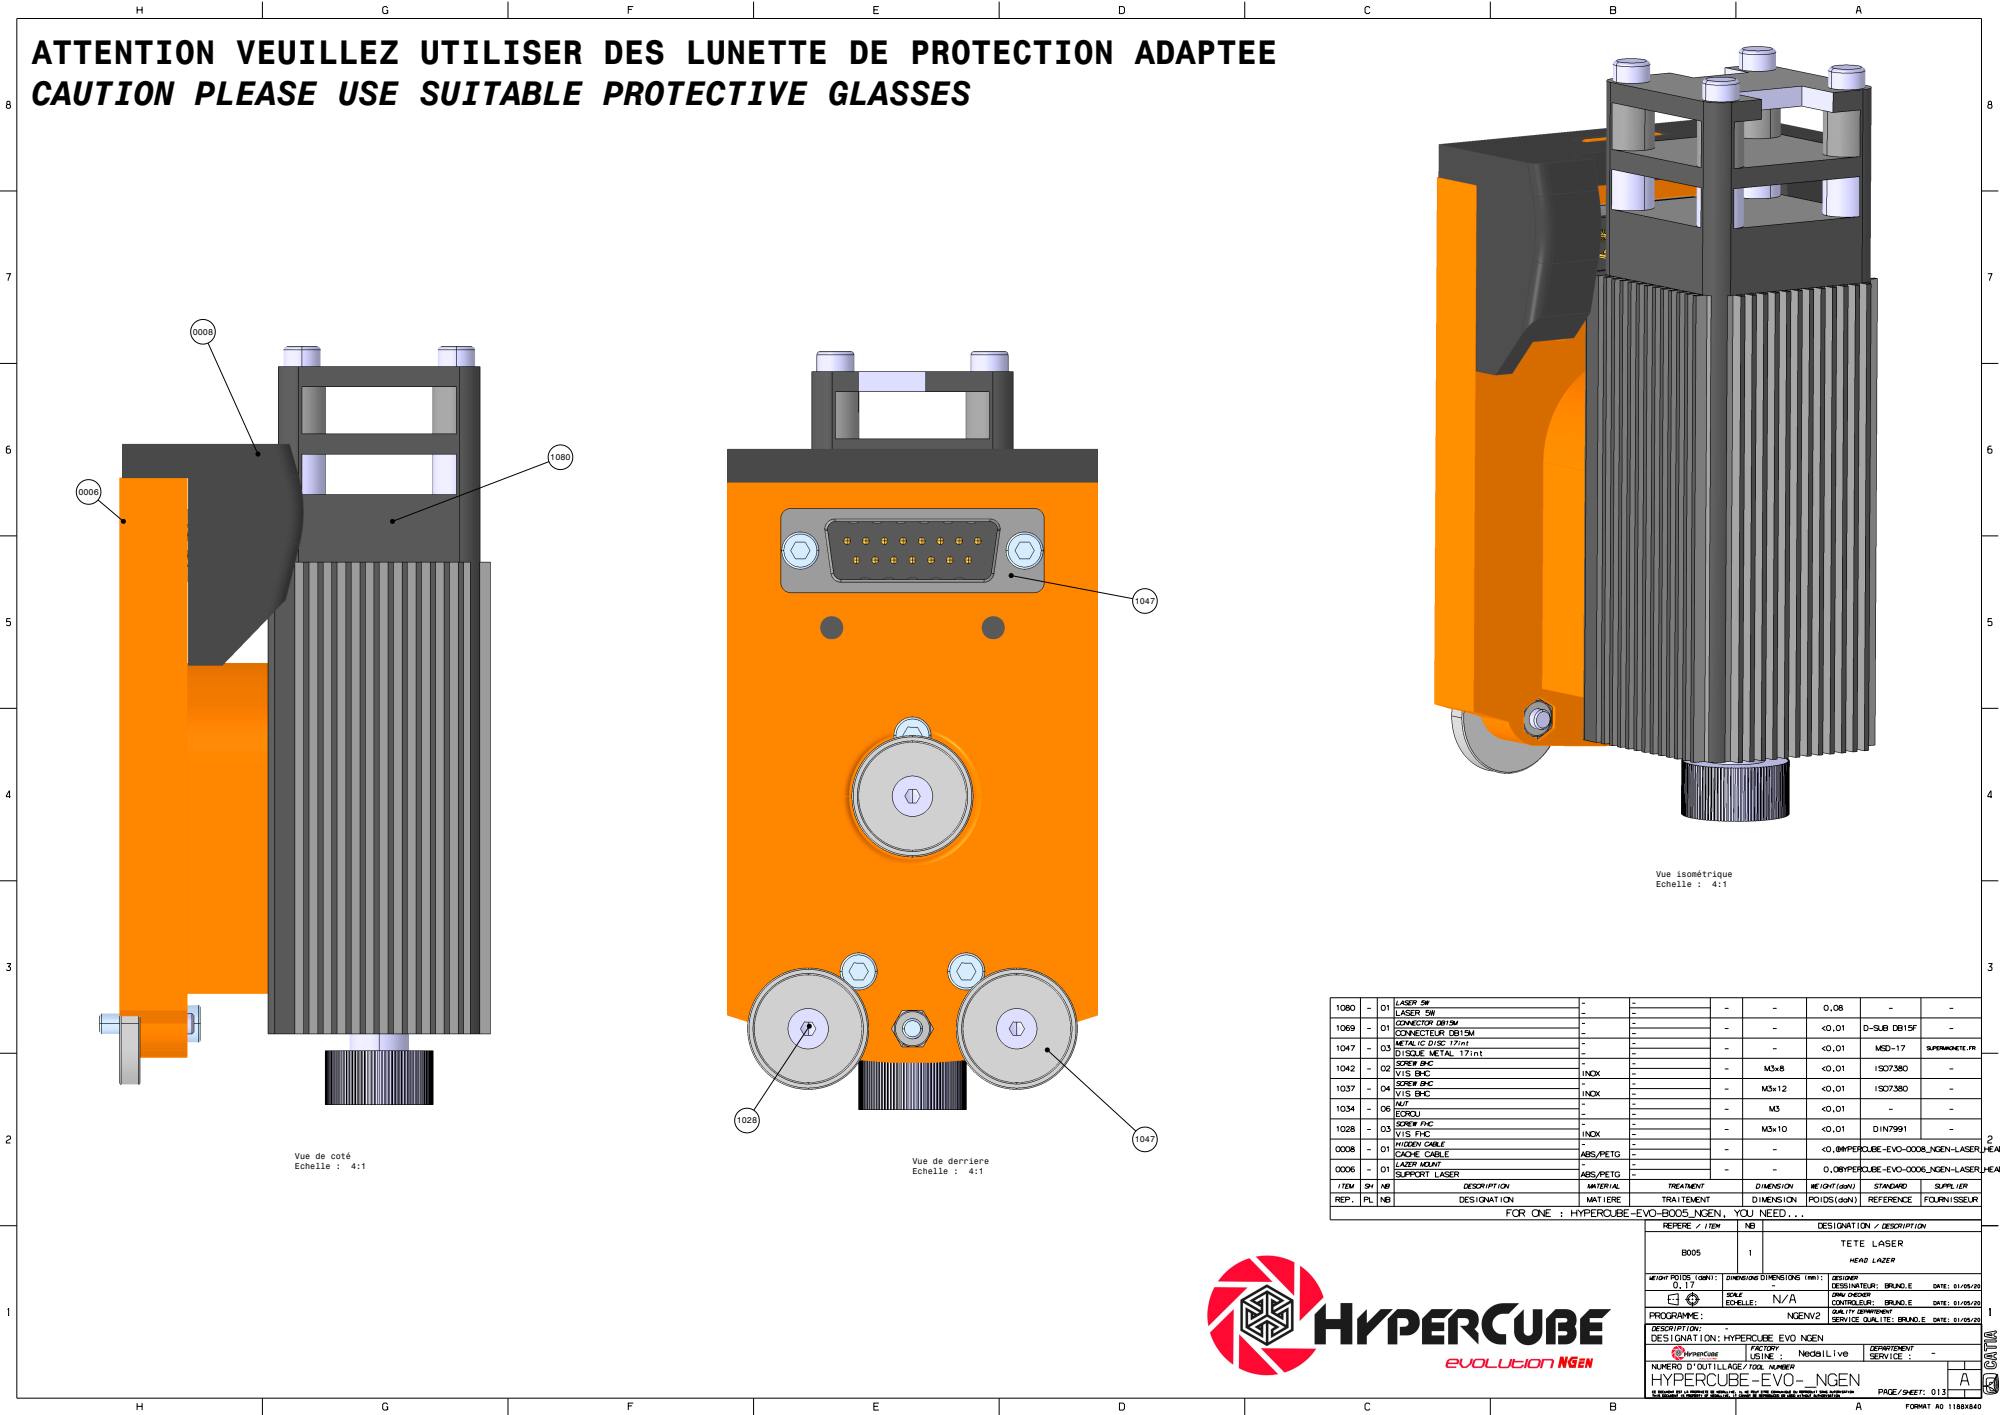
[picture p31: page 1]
Vue isométrique Echelle : 4:1

ATTENTION VEUILLEZ UTILISER DES LUNETTE DE PROTECTION ADAPTEE
CAUTION PLEASE USE SUITABLE PROTECTIVE GLASSES

Vue de coté
Echelle : 4:1

Vue de derriere

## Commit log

2021-01-18 fill the git
    [0002 - CLAMP COURROIE.stl, 0002 - CLAMP.stl, 0003 - TENDEUR DE COURROIE.stl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]
2021-01-18 add optional heads for gen V1
    [5015_Hemera_Shroud_v0.3.stl, 5015_Hemera_Shroud_v0.3_with_bltouch_bracket_v2.stl, BMG_Short_Handle.stl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]
2021-01-18 add optional heads
    [0006-TA1_-_TITAN_AERO_for_NGEN.STL, 0006-TA2_-_FAN_HOLDER_AERO.STL, 0006-TA3_-_CACHE_AERO.STL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]
2021-01-19 Create Pulley & Belt
2021-01-19 correction Readme
    correction typo et mise en forme pour les direct drive
2021-01-19 add step files
    [HYPERCUBE-EVO-B007_D.stp, HYPERCUBE-EVO-B007_G.stp]
2021-01-19 Tete dragon pour chariot V2
    [0006 - SUPPORT TETE PIEZO DRAGON V2.stl, 0007 - CLAMP 30mm TETE DRAGON V2.stl, Orion_dragon.stl]
2021-01-24 Create Chariot Y Pulley bore 5mm
2021-01-24 Create Chariot Y Pulley 5mm bore
2021-01-24 Chariot Y Pulley 5mm bore
    Chariot Y Pulley 5mm bore
    [Chariot Y Left.stl, Chariot Y Right.stl, Flag endstop X.stl]
2021-01-25 add V2 step files
    [HYPERCUBE-EVO-0001_NGEN.stp, HYPERCUBE-EVO-0001_NGEN_V2.stp, HYPERCUBE-EVO-0002_NGEN.stp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]
2021-01-26 Ajout du Zip
    Zip des Fichiers Step pour simplifier le telechargement
    [HYPERCUBE-EVO-0001_NGEN.stp, HYPERCUBE-EVO-0002_NGEN.stp, HYPERCUBE-EVO-0004_NGEN.stp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]
2021-01-27 Maj + CLean 27/01/21
    [0006 - FOR DEVELLOPER.stp, HYPERCUBE-EVO-0001_NGEN.stp, HYPERCUBE-EVO-0001_NGEN_V2.stp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]
2021-01-27 add v2.5 proposal of 0001 part
    [HYPERCUBE-EVO-0001_NGEN_V2.5.step]
2021-01-27 add hemera head for NGEN V2
    [5015_Hemera_Shroud_v0.3.stl, 5015_Hemera_Shroud_v0.3_with_bltouch_bracket_v2.stl, 5015_Matrix_Shroud.stl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]
2021-01-27 add hypercube piezo orion head
    from Dupe Hart
    [Capot_repaired.stl, Clamp_Precision_Orion_repaired.stl, Fan_droit_repaired.stl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]
2021-02-11 maj Diametre roulement
    Mise à jour du diametre 16.4 à 16.2 pour les roulement
2021-02-14 Update
    ajout des support moteur
    [0076L - Support Moteur L.stl, 0076R - Support Moteur R.stl]
2021-02-21 update bom.xlsx
    just added hyperlink
    [Bom.xlsx]
2021-02-21 update version of Y carriage 5mm
    [BOM Chariot Y poulie bore 5mm.xlsm, Chariot Y Left poulie bore 5mm.step, Chariot Y Left poulie bore 5mm.stl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]
2021-02-26 Add files via upload
    rajout de la version 1 de la tête, améliorée pour ressembler à la v2, et avec rajout des boutons de serrage pour les roulements
    [STEP_HYPERCUBE-EVO-0001_NGENv1.5.step, STEP_HYPERCUBE-EVO-0001_NGENv1.5_bouton_serrage_roulement.step]
2021-03-14 Update 14/03/2021
    [12xLames.stl, 12xPions.stl, 1xCone.stl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]
2021-03-21 View of 4 mounts
2021-03-21 update of vue de 4 supports.jpeg
2021-03-24 support for NOVA Hotend
    [HYPERCUBE-EVO-0006_NGEN_NOVA.stl, HYPERCUBE-EVO-0006_NGEN_NOVA.stp, HYPERCUBE-EVO-0007_NGEN_NOVA.stl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]
2021-03-26 support pour tete optionel Nova Hotend & piezo Orion
2021-04-04 Update 04/04/21
    [0008.1_Tirette PushFit_V2.1.stl, 0009_Fan Duct V2_40L.stl, 0009_Fan Duct V2_40R.stl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]
2021-04-04 Update 04/04/2021
    [0008.1_Tirette PushFit_V2.1.stl, 0009_Fan Duct V2_40L.stl, 0009_Fan Duct V2_40R.stl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]
2021-04-29 Revert "Merge branch 'main' of https://github.com/NedalLive/Hypercube-NGen into main"
    This reverts commit cada6b240b8262834930150d54899cd8e6256958, reversing
    changes made to 6d7a51d7b49bd9854182c27651c4352a166aa98c.
    [0008.1_Tirette PushFit_V2.1.stl, 0009_Fan Duct V2_40L.stl, 0009_Fan Duct V2_40R.stl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]
2021-08-18 Nova Hotend & accessories
    [Door Handle.stl, Door Lock.stl, Fan_Duct_L.stl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]
2021-09-02 add picture of nova hotend
